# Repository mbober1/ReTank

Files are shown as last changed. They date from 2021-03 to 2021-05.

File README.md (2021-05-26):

# ReTank - DIY remote controlled tank. :blue_car:
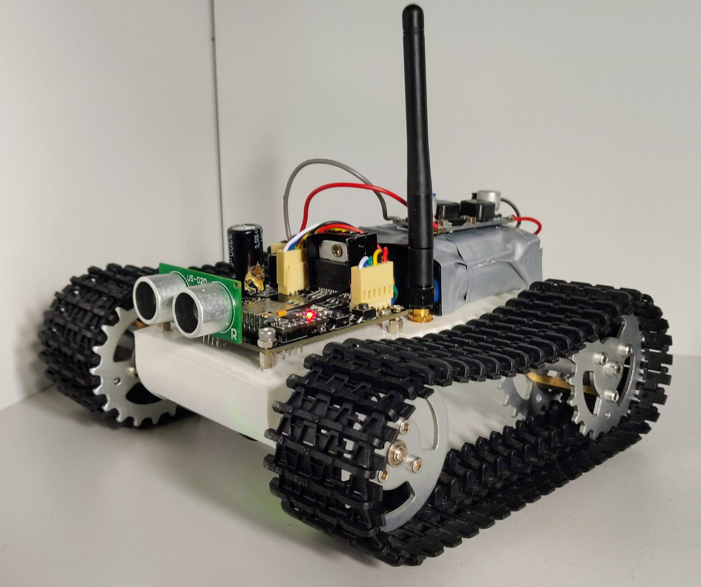
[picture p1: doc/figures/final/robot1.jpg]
alt model


# Usage
## Remote control software
The software controls the robot based on signals sent from the RoboVision program
https://github.com/mbober1/RoboVision

## Features
- [X] DIY energy pack
- [X] WiFi connection
- [X] PID motor power controler
- [X] RoboVision integration
- [X] Circuit board design
- [X] Chassis design

## PCB
Schematic
PCB
PCB2

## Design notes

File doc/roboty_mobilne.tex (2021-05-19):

\documentclass[10pt, a4paper]{article}

\include{preambula}
	
\begin{document}

\def\tablename{Tabela}

\begin{titlepage}
	\begin{center}
		\textsc{\LARGE Projekt}\\[1cm]		
		\textsc{\Large Roboty Mobilne}\\[0.5cm]		
		\rule{\textwidth}{0.08cm}\\[0.4cm]
		{\huge \bfseries Założenia projektowe}\\[1cm]
		{\huge \bfseries Robot gąsienicowy}\\[0.5cm]
		{\huge \bfseries ReTank}\\[0.4cm]
		\rule{\textwidth}{0.08cm}\\[1cm]
		
		\begin{flushright} \large
		\emph{Przygotował:}\\
		Marcin Bober, 249426
		
		\emph{Termin: }srTN18\\[0.4cm]

		\emph{Prowadzący:} \\
		mgr inż. Arkadiusz Mielczarek \\
		
		\end{flushright}
		
		\vfill
		
		{\large \today}
	\end{center}	
\end{titlepage}

\newpage
\tableofcontents
\newpage

\section{Opis projektu}
\label{sec:OpisProjektu}

Projekt dotyczy budowy robota mobilnego, sterowanego zdalnie. 
Zadanie obejmuje zaprojektowanie części elektronicznej, oprogramowania na mikrokontroler i oprogramowania na urządzenie sterujące. 
W skład części elektronicznej wchodzi projekt płytki drukowanej i banku energii.

\section{Bank energii}

\subsection{Ogniwa}

Zasilania robotowi zapewniać będą trzy ogniwa 16850. 
Aby minimalzować koszty, zostały one pozyskane ze starej baterii z laptopa. 
Nie są one dobrze opisane co sprawia że nie jestem w stanie odnaleźć ich specyfikacji.
Ich żywotność również jest nie znana, co uniemożliwia oszacowanie ich łącznej pojemności.

\begin{figure}[H]
	\centering
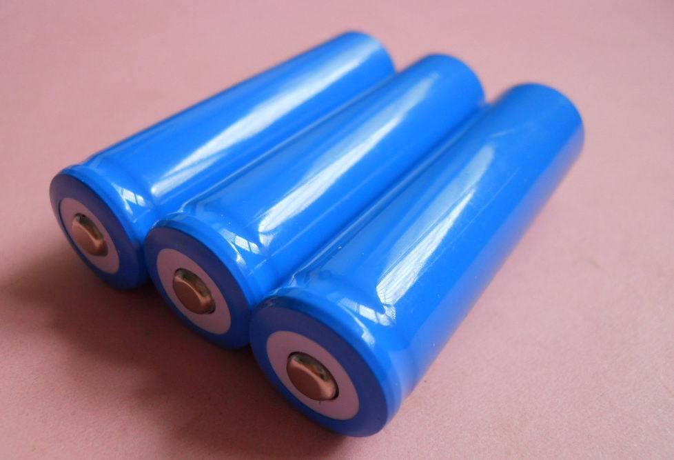
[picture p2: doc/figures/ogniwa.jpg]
	
	\caption{Ogniwa 16850}
	\label{fig:ogniwa}
\end{figure}

\subsection{Balanser}

Do zarządzania ogniwami użyty zostanie gotowy układ BMS przystosowany do współpracy z trzema ogniwami 16850. 
Zapewnia on podstawowe zabezpieczenia w tym:

\begin{itemize}
	\item zabezpieczenie przed nadmiernym rozładowaniem poniżej 3.0V,
	\item zabezpieczenie przed przeładowaniem powyżej 4.25V,
	\item zabezpieczenie przed przeciążeniem prądowym,
	\item zabezpieczenie przed zwarciem.
\end{itemize}

Napięcie generowane przez baterię ogniw powinno oscylować w zakresie 9.0V - 12.7V

\begin{figure}[H]
	\centering
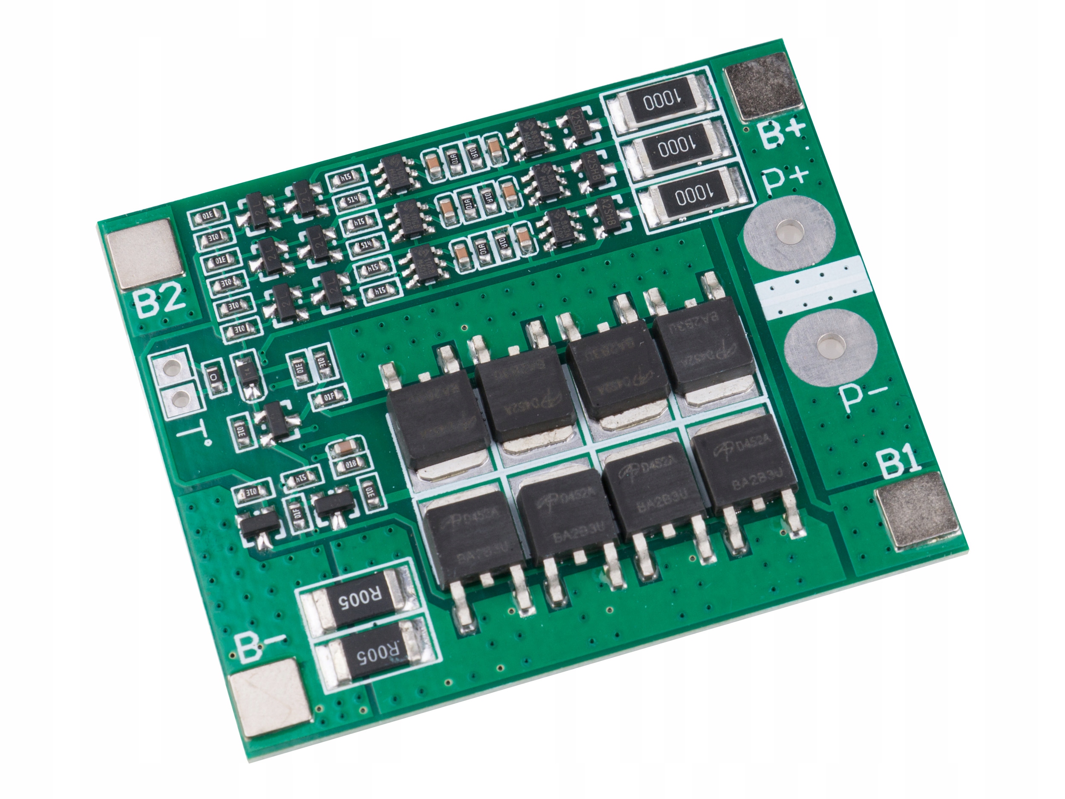
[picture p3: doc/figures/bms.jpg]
	
	\caption{Balanser baterii}
	\label{fig:bms}
\end{figure}

\section{Płytka drukowana}
Jednym z podstawowych elementów projektu jest stworzenie płytki drukowanej integrującej wszystkie wymagane elementy.

\subsection{Mikrokontroler}
Sercem układu zostanie układ ESP32-WROVER. 
Najważniejszym kryterium decydującym o wyborze tego konkretnego układu jest wbudowany modu WiFi i jego niska cena oscylująca w okolicach 2.50\$.
Jest to zdecydowanie najtańszy sposób na połączenia robota do Internetu.

\begin{figure}[H]
	\centering
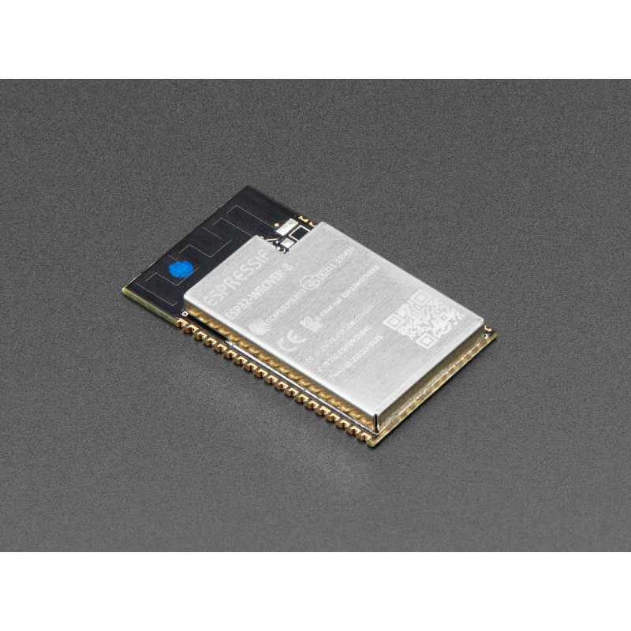
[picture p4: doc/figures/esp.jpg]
	
	\caption{Mikrokontroler ESP32}
	\label{fig:esp32}
\end{figure}

Najważniejsze cechy:
\begin{itemize}
	\item Wbudowany MCU o dwóch rdzeniach z taktowaniem do 240 MHz
	\item Protokoły Wi-Fi: 802.11 b/g/n/d/e/i/k/r
	\item Protokoły BT: Bluetooth v4.2 BR/EDR oraz Bluetooth BLE
	\item Napięcie zasilania: 2.2 V - 3.6 V
	\item Średni pobór prądu: 80 mA
\end{itemize}

\subsection{Sterowniki silników}
Układ będzie wspierał sterowanie dwoma silnikami prądu stałego. 
Każdy z nich będzie mógłbyć wyposarzony w osobny enkoder liczący obroty silnika.
Do tego celu posłuży układa L298N w obudowie Multiwatt 15 pin.

\begin{figure}[H]
	\centering
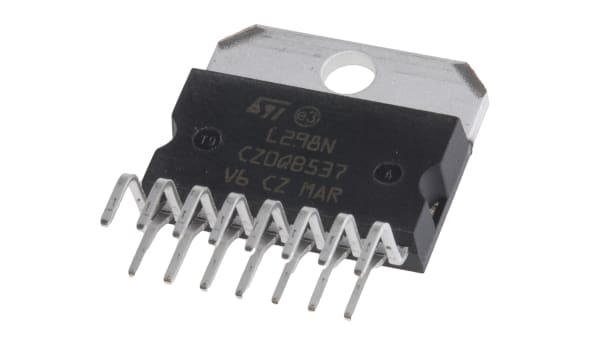
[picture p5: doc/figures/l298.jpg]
	
	\caption{Układ scalony L298N}
	\label{fig:l298n}
\end{figure}

\subsection{Akcelereometr}
Robot będzie wyposarzony w akcelerometr i żyroskop, aby móc mierzyć przyspieszenia oraz prędkości kątowe.
Będzie to możliwe dzięki użyciu układu MPU-6050.

\begin{figure}[H]
	\centering
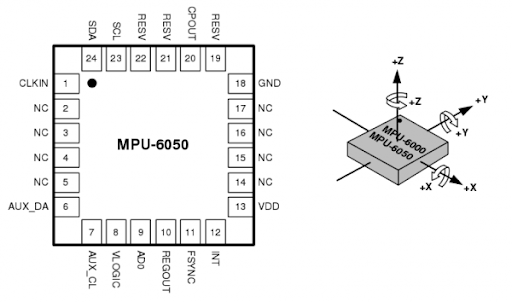
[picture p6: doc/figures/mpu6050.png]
	
	\caption{Układ scalony MPU6050}
	\label{fig:mpu6050}
\end{figure}

\subsection{Inne}
Aby móc komfortowo użytkować i prototypować robota niezbędne będą dodatkowe elementy takie jak:
\begin{itemize}
	\item wyprowadzenie JATG,
	\item wyprowadzenie interfejsu I2C,
	\item wyprowadzenie kamery ArduCam OV2640,
	\item wyprowadzenie UART,
	\item wejście zasilania,
	\item złącze czujnika ultradzwiękowego,
	\item dwa wejścia enkoderów,
	\item dwa wyjścia na silniki.
\end{itemize}

\section{Mechanika}
\subsection{Podwozie}
Aby zredukować koszty i lepiej zintegrować wszystkie elementy ze sobą,
postanowiłem samemu zaprojektować podwozie i wydrukować je przy użyciu drukarki 3D.
Materiał który do tego użyję to ABS.
% Na początku planowania projektu miałem zamiar zaprojektować własne podwozie, 
% ale koszty silników z enkoderami były bardzo duże. Bardziej opłacalne okazały się gotowe zestawy,
% więc zdecydowałem że jako podwozie zostanie użyty zestaw "4WD Smart Robot Car Chassis Kits".
% Jest to najbardziej opłacalne rozwiązanie.

\subsection{Silniki}
Silniki których użyję są produkcji DFRobot. Mają one doczepione enkodery, 
które pozwolą mi bardzo dokładnie kontorlować prędkości silników.
\begin{figure}[H]
	\centering
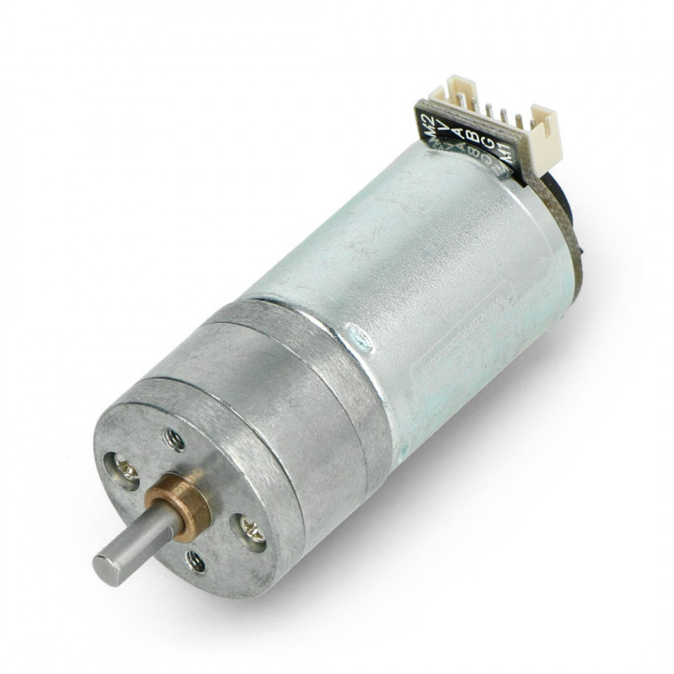
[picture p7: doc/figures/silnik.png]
	
	\caption{Silnik z enkoderem}
	\label{fig:silnk}
\end{figure}

Ich skrócona specyfikacja:
\begin{itemize}
	\item Napięcie zasilania: 6 V
	\item Napięcie enkodera: od 3,3 V do 5 V
	\item Współczynnik redukcji: 1:20
	\item Prędkość bez obciążenia: 300 RPM - 0,1 A
\end{itemize}

\section{Harmonogram}
\begin{enumerate}
	\item Sporządzenie listy i zdobycie wymaganych elementów. (17.03)
	\item Zaprojektowanie i wykonanie podwozia. (24.03)
	\item Zaprojektowanie i wykonanie pakietu baterii. (31.03)
	\item Zaprojektowanie płytki drukowanej. (7.04)
	\item Napisanie i przetestowanie bazowej wersji programu na MCU. (14.04)
	\item Zbudowanie komunikacji z kontrolerem. (21.04)
	\item Dodanie obsługi enkoderów. (28.04)
	\item Dodanie obsługi żyroskopu. (5.05)
	\item Testowanie i dopieszczanie. (12.05)
\end{enumerate}

\section{Podwozie}
Podwozie zostało zaprojektowane w programie Fusion360. 
Pierwsza wersja cierpiała na problemy związane z małą sztywnością 
konstrukcji, co znacząco wpływało na jakość sterowania. 
Z tego też powodu została zaprojektowana druga, znacznie wytrzymalsza
wersja podwozia.

\begin{figure}[H]
	\centering
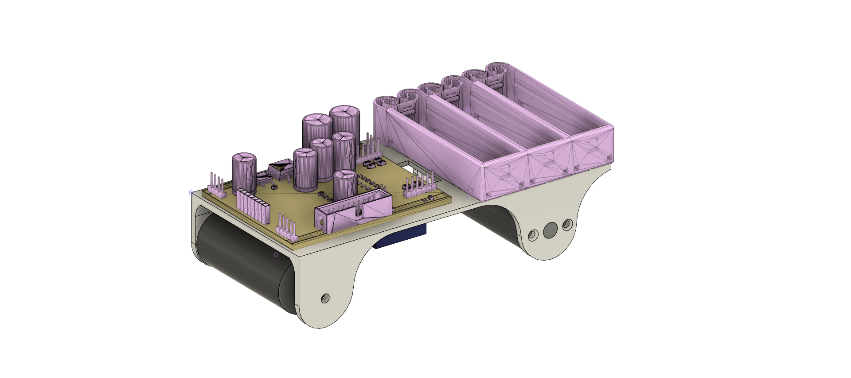
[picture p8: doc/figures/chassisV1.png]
	
	\caption{Pierwsza wersja podwozia}
	\label{fig:chassisv1}
\end{figure}

\begin{figure}[H]
	\centering
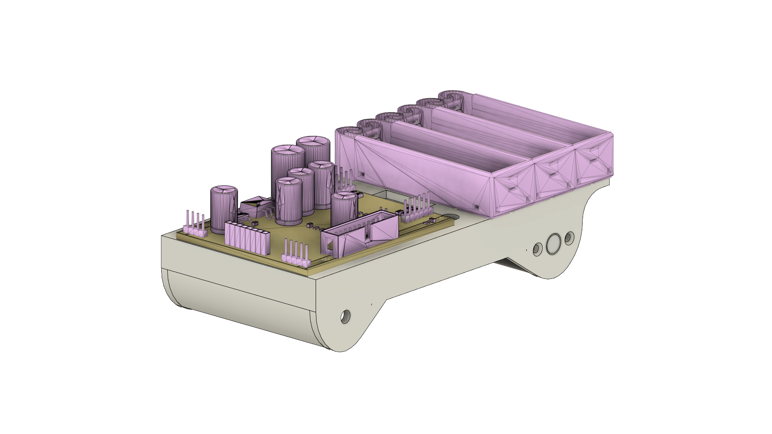
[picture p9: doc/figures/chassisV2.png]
	
	\caption{Druga wersja podwozia}
	\label{fig:chassisv2}
\end{figure}

\section{Płytka drukowana}
W celu zwiększenia jakości i poprawy niezawodności projektu, 
została zaprojektowana płytka drukowana, która ma za zadanie
integrować wszystkie niezbędne peryferia i minimalzować zajmowane miejsce. 

\begin{figure}[H]
	\centering
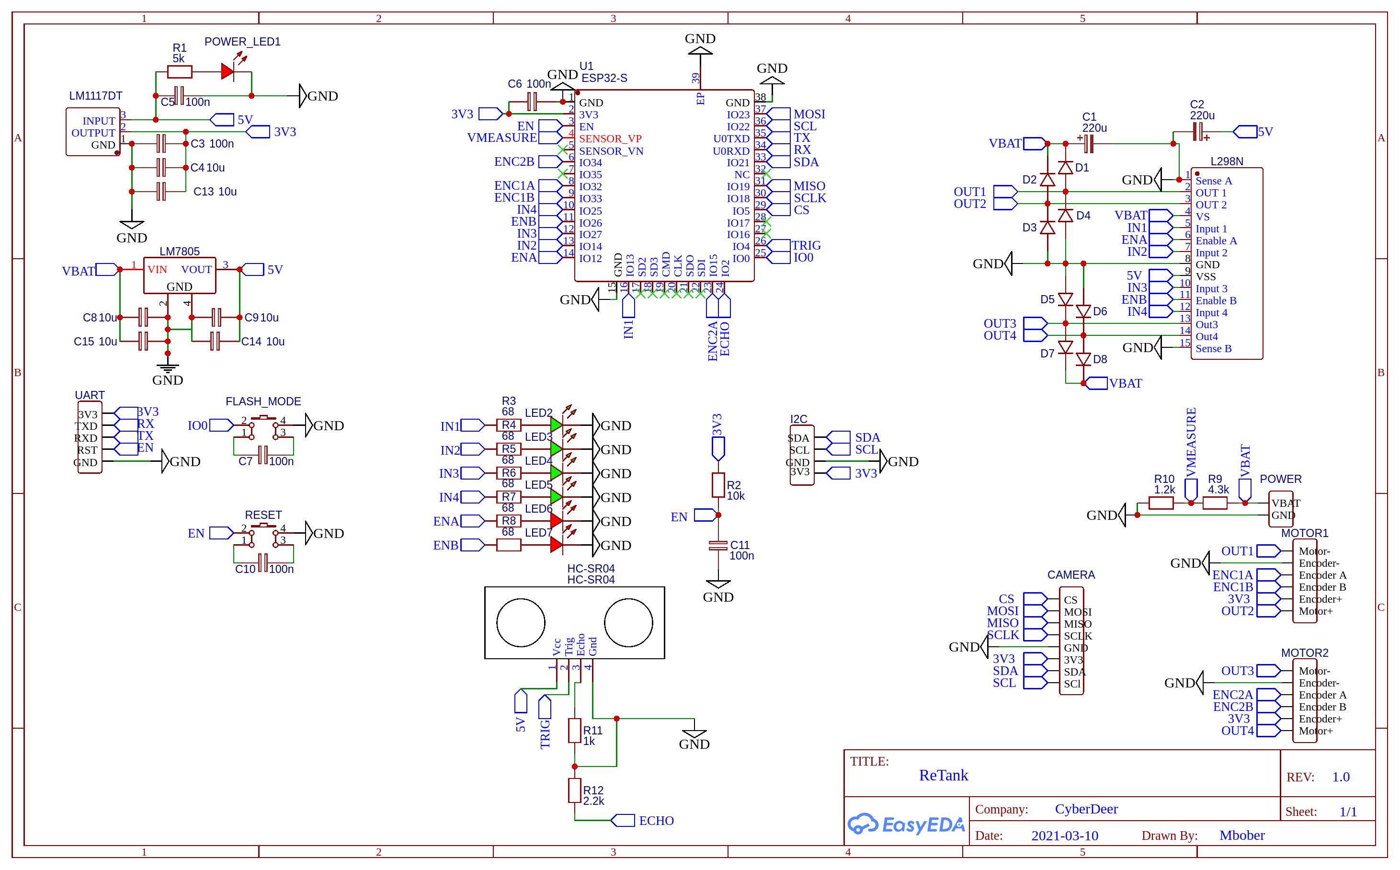
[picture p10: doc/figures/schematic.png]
	
	\caption{Schemat połączeń}
	\label{fig:schematic}
\end{figure}

2021-04-16 zostało złożone zamówienie na 5 sztuk płytek.
Zamówienie jest jeszcze w trakcie transportu. Ostateczną wersję 
można zobaczyć poniżej. Z powodu ograniczonej przestrzeni i
niewystarczającej liczby pinów mikrokontrolera, zrezygnowałem z
portu JTAG.

\begin{figure}[H]
	\centering
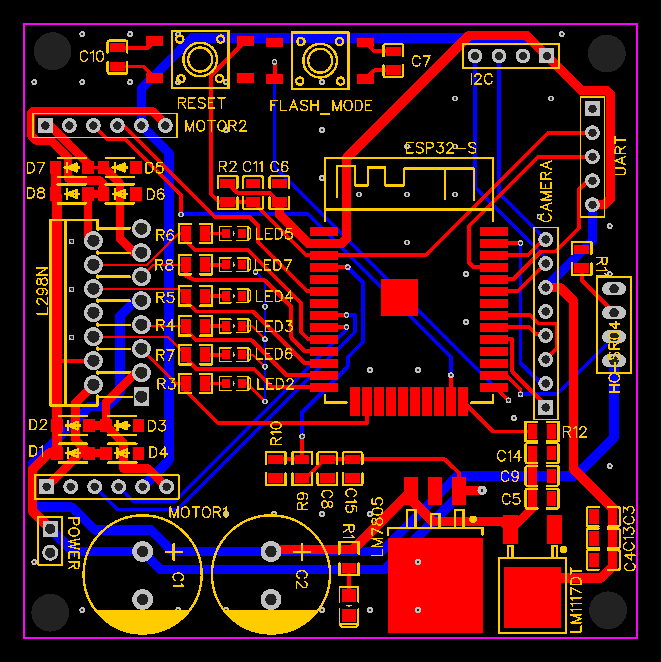
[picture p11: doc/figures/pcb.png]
	
	\caption{PCB}
	\label{fig:pcb}
\end{figure}

\section{Program}
Program na mikrokontroler został napisany z użyciem warstwy abstrakcji
ESP-IDF, udostępnionej przez producenta układu. Dla zwiększenia 
możliwości sprzętu, zdecydowałem się na użycie systemu czasu rzeczywistego
FreeRTOS. Dzięki temu kod został podzielony na oddzielne moduły, 
a każdy z nich pracuje na swoim odrębnym wątku. Pozwoliło to również
ustawiać wyższy piorytet funkcjom, które mają krytyczny wpływ na dzianie robota.
Komunikacja międzyprocesowa została zrealizowana poprzez kolejki piorytetowe,
co znacząco usprawnia cały proces.

Całość kodu dostępna jest w moim repozytorium na
\href{https://github.com/mbober1/ReTank}{GitHub}.

\section{Komunikacja z robotem}

Połączenie z robotem odbywa się poprzez sieć WiFi. W pierwszej kolejności 
nawiązywane jest połączenie przy użyciu protokołu TCP. Jeśli się ono powiedzie
to uruchamiana jest dodatkowa transmicja z wykorzystaniem UDP. 
Dzięki takiej koncepcji mamy dwa niezależne kanały komunikacji. Pierwszy służy
do przesyłania danych które mają niski piorytet czasowy, potrzebują potwierdzenia
odebrania i ewentualnej retransmisji danych. Druga droga komunikacji powstała, 
aby przesyłać ciągły strumień nowych danych. Zależy nam na jaknajniższym opóźnieniu,
a ewentualny błąd trasmisji nie jest krytyczny, bo inforamcje te szybko się 
przedawniają i są zastępowane przez nowe, świeższe. \newline

Każda ramka zaczyna się od wybranej dużej litery alfabetu, określającej rodzaj 
przesyłanych danych. Dla protokołu TCP są to:

	\begin{itemize}
	  \item P - ping,
	  \item D - dystans przeszkody,
	  \item B - bateria,
	  \item S - realna predkość.
	\end{itemize}
	
Natomiast dla protokołu UDP wyróżniamy:
  \begin{itemize}
	\item E - moc silników,
	\item A - akcelometr,
	\item G - żyroskop.
  \end{itemize}

Wszystkie paczki danych zakończone są średnikiem, przed którym znajduje się
ośmiobitowy cykliczny kod nadmiarowy. Niestety ze względu na róźnorodność 
transmitownych informacji, w tym miejscu kończą się cechy wspólne poszczególnych 
ramek.

\subsection{Ping}
Jest to najprostrza z obecych tu ramek. Nie przenosi żadnych informacji.
Oznacza jedynie koniecność odesłania do nadawcy identyczniej wiadomości,
aby można było wyznaczyć chwilę czasowe, niezbędne do obliczenia opóźnienia
transmisji.

Forma ramki to: $P\#;$

Gdzie \# oznacza CRC.

\subsection{Dystans przeszkody}
Przesyła informacje z robota o odległości odczytanej z czujnika ultradzwiękowego.

Forma ramki to: $D<uint8\_t>\#$;
\newline

Gdzie \# oznacza CRC. Przed nim znajduje się wartość odległości wyrażonej 
w centymetrach, w zakresie 0-100cm.

\subsection{Bateria}
Przesyła informacje z robota o poziomie baterii.

Forma ramki to: $B<uint8\_t>\#$;
\newline

Gdzie \# oznacza CRC. Przed nim znajduje się poziom baterii wyrażonej 
w procentach, w zakresie 0-100\%.

\subsection{Prędkość}
Przesyła informacje z robota o prędkości na kołach.

Forma ramki to: $S<uint8\_t> <uint8\_t>\#$;
\newline

Gdzie \# oznacza CRC. Przed nim znajdujdują się dwie wartości oddzielone spacją
odnoszące się do prędkości poszczególnych kół wyrażonej w metrach na sekunde.

\subsection{Moc silników}
Przesyła informacje z aplikacji do robota o zadanej mocy silników.

Forma ramki to: $E<uint8\_t> <uint8\_t>\#$;
\newline

Gdzie \# oznacza CRC. Przed nim znajdujdują się dwie wartości oddzielone spacją
odnoszące się do zadanej mocy poszczególnych kół wyrażonej w procentach.
Zakresy tych wartości musza mieścić się od 0 do 100\%

\subsection{Akcelometr}
Przesyła informacje z robota o aktualnych wskazaniach akcelometru.

Forma ramki to: $A<uint8\_t> <uint8\_t> <uint8\_t>\#$;
\newline

Gdzie \# oznacza CRC. Przed nim znajdujdują się trzy wartości oddzielone spacją
odnoszące się do aktualnych wskazań akcelometru.

\subsection{Żyroskop}
Przesyła informacje z robota o aktualnych wskazaniach żyroskopu.

Forma ramki to: $G<uint8\_t> <uint8\_t> <uint8\_t>\#$;
\newline

Gdzie \# oznacza CRC. Przed nim znajdujdują się trzy wartości oddzielone spacją
odnoszące się do aktualnych wskazań żyroskopu.

\section{Aplikacja do komunikacji}
Rezultaty komunikacji z komputerem i działania całego projektu możemy z
łatwością podziwiać z pomocą mojej specialnie przygotowanej aplikacji w QT
dostępnej w moim repozytorium na
\href{https://github.com/mbober1/RoboVision}{GitHub}.

\begin{figure}[H]
	\centering
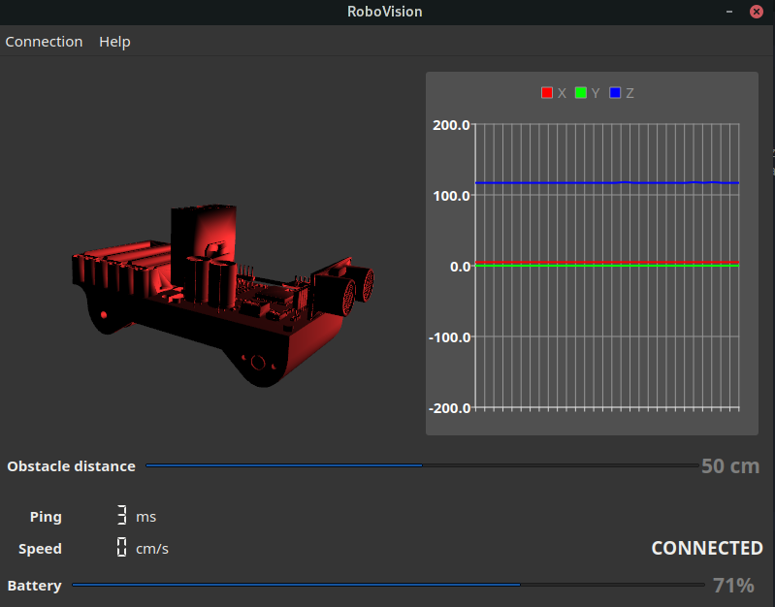
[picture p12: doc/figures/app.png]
	
	\caption{Aplikacja RoboVision}
	\label{fig:app}
\end{figure}

\begin{figure}[H]
	\centering
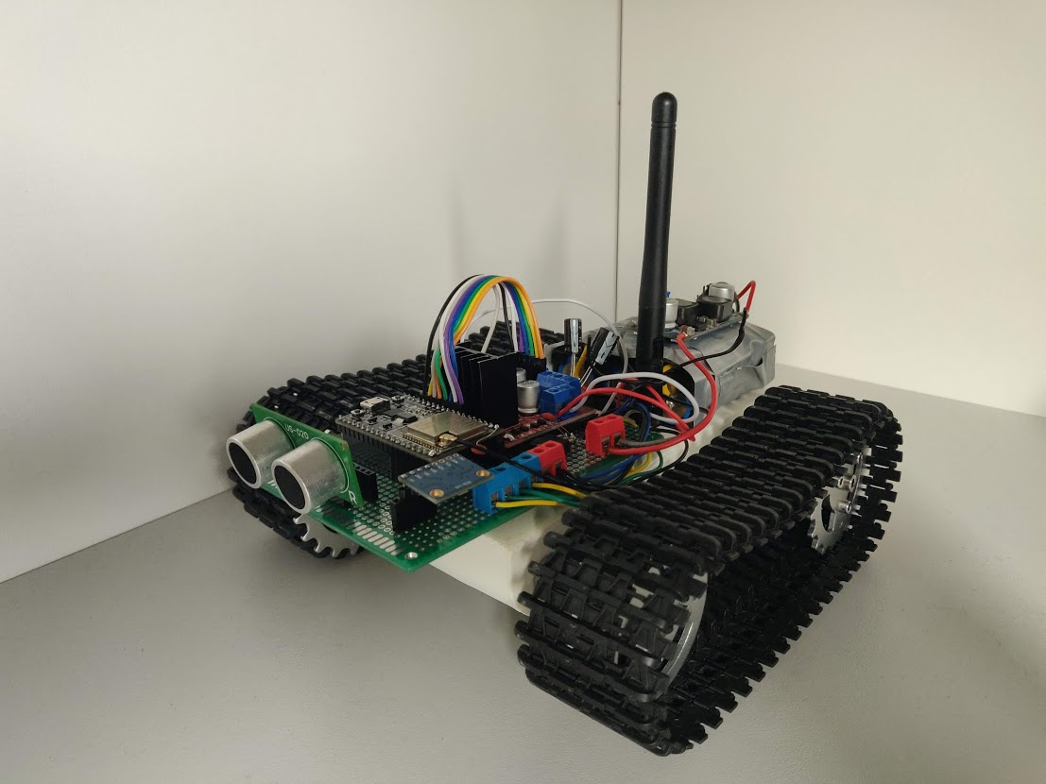
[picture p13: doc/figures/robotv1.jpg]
	
	\caption{Prototyp robota}
	\label{fig:robot}
\end{figure}

\section{Rezultat}
Projekt robota został zakończony sukcesem. Wszystkie problemy z jakimi borykały
się prototypy zostały wyeliminowane. Można więc uznać projekt za zamknięty.  

\begin{figure}[H]
	\centering
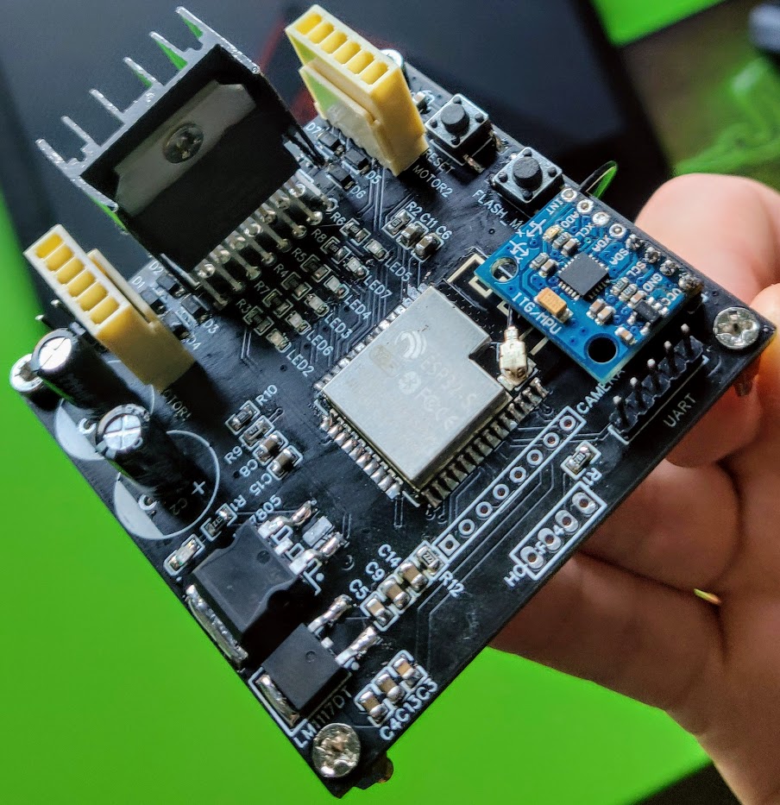
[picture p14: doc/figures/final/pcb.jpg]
	
	\caption{Ostateczna wersja płytki drukowanej}
	\label{fig:pcb_final}
\end{figure}

\begin{figure}[H]
	\centering
	
	\caption{Ostateczna wersja robota}
	\label{fig:robot_final1}
\end{figure}

\begin{figure}[H]
	\centering
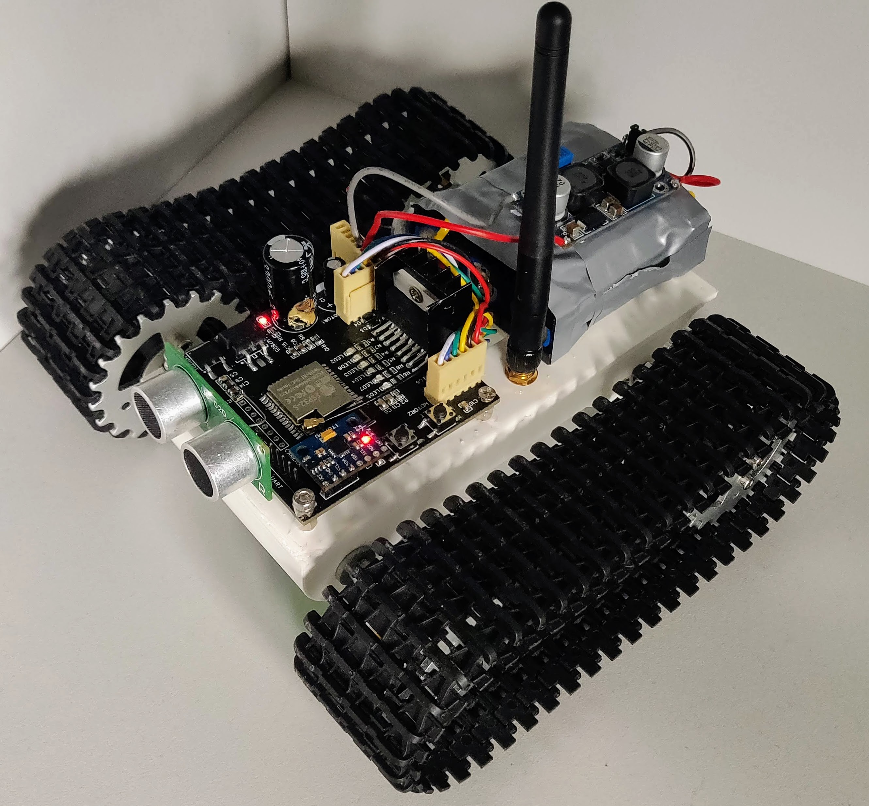
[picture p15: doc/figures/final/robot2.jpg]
	
	\caption{Ostateczna wersja robota}
	\label{fig:robot_final2}
\end{figure}

\begin{figure}[H]
	\centering
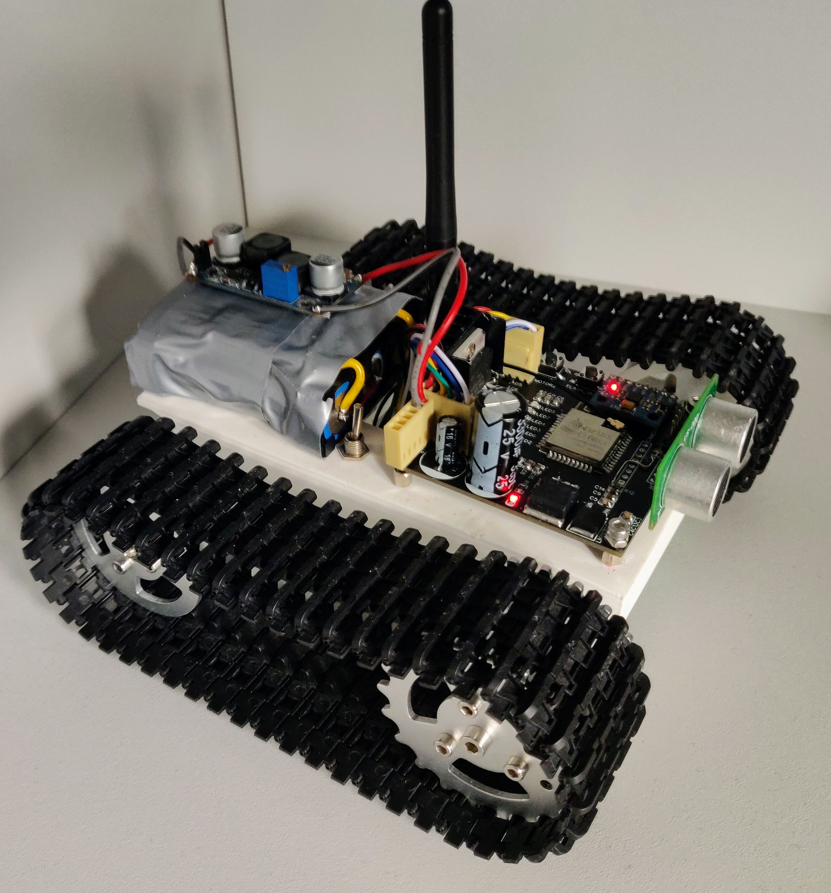
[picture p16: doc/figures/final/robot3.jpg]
	
	\caption{Ostateczna wersja robota}
	\label{fig:robot_final3}
\end{figure}

\begin{figure}[H]
	\centering
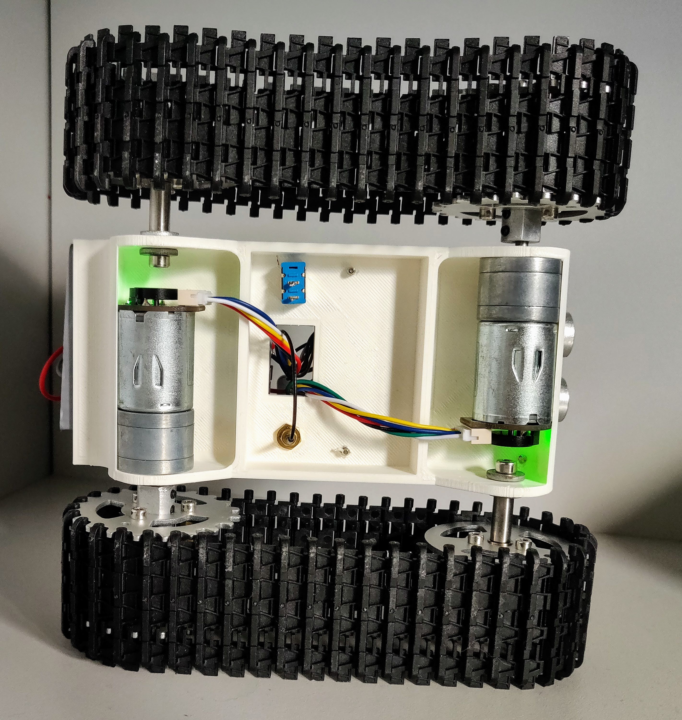
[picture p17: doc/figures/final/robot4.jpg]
	
	\caption{Ostateczna wersja robota}
	\label{fig:robot_final4}
\end{figure}

\end{document}

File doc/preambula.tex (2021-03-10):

%Preambuła dokumentu

% linki w spisie tresci, bibliografi
\usepackage[bookmarks=true,bookmarksnumbered=false,unicode=true,pdftex=true, colorlinks,filecolor=black,linkcolor=black,urlcolor=black,citecolor=black]{hyperref}

%ustawienie rozmiaru papieru
\usepackage[a4paper, left=2.5cm, right=2.5cm, top=2.5cm, bottom=2.5cm, headsep=1.2cm]{geometry}

%rozmaite ustawienia pozwalające okreslić język

%NALEŻY wybrać jeden z pakietów
%\usepackage{polski} %przydatne podczas składania dokumentów w j. polskim
\usepackage[polish]{babel}  % pakiet lokalizujący dokument w języku polskim
%\usepackage[british]{babel}

\usepackage{indentfirst}	% polski styl pisania (np. rozpoczecie pierwszego akapitu
% pod nazwa rozdzialu od wciecia)
%\usepackage[OT4]{fontenc}
\usepackage[utf8]{inputenc} % w miejsce utf8 można wpisać latin2 bądź cp1250,
% w zależności od tego w jaki sposób kodowane są 
% polskie znaki diakrytyczne przy wprowadzaniu 
% z klawiatury.
%kodowanie znaków, zależne od systemu
\usepackage[T1]{fontenc} %poprawne składanie polskich czcionek

%OPEROWANIE NA OBRAZACH
\usepackage{graphicx}       % pakiet graficzny, umożliwiający m.in.
% import grafik w formacie eps
%\usepackage{epstopdf}		% pozwala na importowanie grafik w formacie eps
% przy użyciu pdflatex
\usepackage[update,prepend]{epstopdf}
\usepackage{rotating}       % pakiet umożliwiający obracanie rysunków
\usepackage{subfigure}      % pakiet umożliwiający tworzenie podrysunków
\usepackage{epic}           % pakiet umożliwiający rysowanie w środowisku latex
\usepackage{psfrag}         % pakiet umożliwiający podmianę łańcuchów znaków 
% w plikach eps
%\usepackage{curves}         % pakiet do wykreslania krzywych

%pakiety dodające dużo dodatkowych poleceń matematycznych
\usepackage{amsfonts}       % pakiet z rozmaitymi czcionkami matematycznymi
%\usepackage{amssymb}        % pakiet z rozmaitymi symbolami matematycznymi
\usepackage{amsmath}        % pakiet z rozmaitymi środowiskami matematycznymi

\usepackage{fp}             % pakiet z funkcjami operujacymi 
% na liczbach zmiennoprzecinkowych
\usepackage{calc}           % pakiet umożliwiający operacje arytmetyczne
% na tzw. licznikach (liczbach całkowitych)
\usepackage{leftidx}		% indeksy górne i dolne po lewej stronie

%definicje matematyczne
\providecommand{\abs}[1]{\lvert#1\rvert}
\providecommand{\norm}[1]{\lVert#1\rVert}

%pakiety wspomagające i poprawiające składanie tabel
\usepackage{supertabular}
\usepackage{array}
\usepackage{tabularx}
\usepackage{hhline}
\usepackage{longtable}		% wsparcie dla dlugich tabel
\usepackage{multicol}		% podzial strony na wiele kolumn

%pakiet do BibTex
\usepackage{cite}

\usepackage{url} %pakiet pozawalający na dodawanie adresów url w bibliografi

%pakiet wypisujący na marginesie etykiety równań i rysunków zdefiniowanych przez \label{}, chcąc wygenerować finalną wersję dokumentu wystarczy usunąć poniższą linię
%\usepackage{showlabels}

\usepackage{float}			% lepsza obsluga mechanizmow obiektow plywajacych
% wymuszenie wstawienia np. tabeli, obrazka w danym miejscu przez [H]

\usepackage{listings}       % pakiet dedykowany zrodlom programow
\usepackage{color}

\definecolor{dkgreen}{rgb}{0,0.6,0}
\definecolor{gray}{rgb}{0.5,0.5,0.5}
\definecolor{mauve}{rgb}{0.58,0,0.82}

\lstset{ %
	language=C,                % the language of the code
	basicstyle=\small,           % the size of the fonts that are used for the code
	numbers=left,                   % where to put the line-numbers
	numberstyle=\footnotesize\color{gray},  % the style that is used for the line-numbers
	stepnumber=1,                   % the step between two line-numbers. If it's 1, each line 
	% will be numbered
	numbersep=5pt,                  % how far the line-numbers are from the code
	backgroundcolor=\color{white},      % choose the background color. You must add \usepackage{color}
	showspaces=false,               % show spaces adding particular underscores
	showstringspaces=false,         % underline spaces within strings
	showtabs=false,                 % show tabs within strings adding particular underscores
	%frame=single,                   % adds a frame around the code
	rulecolor=\color{black},        % if not set, the frame-color may be changed on line-breaks within not-black text (e.g. comments (green here))
	tabsize=2,                      % sets default tabsize to 2 spaces
	captionpos=b,                   % sets the caption-position to bottom
	breaklines=true,                % sets automatic line breaking
	breakatwhitespace=false,        % sets if automatic breaks should only happen at whitespace
	%title=\lstname,                   % show the filename of files included with \lstinputlisting;
	% also try caption instead of title
	keywordstyle=\color{blue},          % keyword style
	commentstyle=\color{dkgreen},       % comment style
	stringstyle=\color{mauve},         % string literal style
	escapeinside={\%*}{*)},            % if you want to add LaTeX within your code
	morekeywords={*,...},              % if you want to add more keywords to the set
	deletekeywords={...}              % if you want to delete keywords from the given language
}

%polish signs in lst code
\lstset{literate=%
	{ą}{{\k{a}}}1
	{ć}{{\'c}}1
	{ę}{{\k{e}}}1
	{ł}{{\l}}1
	{ń}{{\'n}}1
	{ó}{{\'o}}1
	{ś}{{\'s}}1
	{ż}{{\.z}}1
	{ź}{{\'z}}1
	{Ą}{{\k{A}}}1
	{Ć}{{\'C}}1
	{Ę}{{\k{E}}}1
	{Ł}{{\L}}1
	{Ń}{{\'N}}1
	{Ó}{{\'O}}1
	{Ś}{{\'S}}1
	{Ż}{{\.Z}}1
	{Ź}{{\'Z}}1
}

\usepackage{verbatim}       % pakiet dedykowany rozmaitym wydrukom tekstowym
\usepackage{ifthen}         % pakiet umożliwiający tworzenie prostych programów
% (m.in. zawiera instrukcje powtórzeniowe 
% i warunkowe)
\usepackage{upquote}		%normal quotations marks ' and `

% deklaracje wymagane przez pakiet theorem automatycznie ladowany w przypadku
% klasy dokumentu article
%
\newtheorem{Dn}{Definicja}[section]     % deklaracja srodowiska definicja
\newtheorem{La}[Dn]{Lemat}                % deklaracja srodowiska lemat
\newtheorem{Tm}[Dn]{Twierdzenie}          % deklaracja srodowiska twierdzenie
\newtheorem{Rk}[Dn]{Spostrze{\.z}enie}  % deklaracja srodowiska spostrzezenie
\newtheorem{Am}[Dn]{Algorytm}           % deklaracja srodowiska algorytm
\newtheorem{As}[Dn]{Za{\l}o{\.z}enie}   % deklaracja srodowiska zalozenie
\newtheorem{Pn}[Dn]{Propozycja}           % deklaracja srodowiska propozycja
\newtheorem{Py}[Dn]{W{\l}asno{\'s}{\'c}}  % deklaracja srodowiska wlasnosc
\newtheorem{Cy}[Dn]{Wniosek}              % deklaracja srodowiska wniosek
\newtheorem{Ee}[Dn]{Przyk{\l}ad}        % deklaracja srodowiska przyklad
\newtheorem{Ex}{{\'C}wiczenie}          % deklaracja srodowiska cwiczenie

%helps to specify width of a column in table
%\begin{tabular}{|C{1cm}|c|c|c|c|c|c|c|c|c|c|}
%first column will have widht of 1cm
\newcolumntype{L}[1]{>{\raggedright\let\newline\\\arraybackslash\hspace{0pt}}m{#1}}
\newcolumntype{C}[1]{>{\centering\let\newline\\\arraybackslash\hspace{0pt}}m{#1}}
\newcolumntype{R}[1]{>{\raggedleft\let\newline\\\arraybackslash\hspace{0pt}}m{#1}}

\sloppy			%zawija bardzo długie linie

%\pagenumbering{gobble}% Remove page numbers (and reset to 1)

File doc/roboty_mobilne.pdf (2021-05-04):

Projekt

Roboty Mobilne

# Założenia projektowe

# Robot gąsienicowy

# ReTank

Przygotował:
Marcin Bober, 249426
Termin: srTN18

Prowadzący:
mgr inż. Arkadiusz Mielczarek

4 maja 2021

## Spis treści

1 Opis projektu | 2
2 Bank energii | 2
3 Płytka drukowana | 3
4 Mechanika | 5
5 Harmonogram | 6
6 Podwozie | 6
7 Płytka drukowana | 7
8 Program | 8
9 Komunikacja z robotem | 8
10 Aplikacja do komunikacji | 10
11 Aktualne rezultaty | 10

## 1 Opis projektu

Projekt dotyczy budowy robota mobilnego, sterowanego zdalnie. Zadanie obejmuje zaprojektowanie części elektronicznej, oprogramowania na mikrokontroler i oprogramowania na urządzenie sterujące. W skład części elektronicznej wchodzi projekt płytki drukowanej i banku energii.

## 2 Bank energii

### 2.1 Ogniwa

Zasilania robotowi zapewniać będą trzy ogniwa 16850. Aby minimalzować koszty, zostały one pozyskane ze starej baterii z laptopa. Nie są one dobrze opisane co sprawia że nie jestem w stanie odnaleźć ich specyfikacji. Ich żywotność również jest nie znana, co uniemożliwia oszacowanie ich łącznej pojemności.


Rysunek 1: Ogniwa 16850

### 2.2 Balanser

Do zarządzania ogniwami użyty zostanie gotowy układ BMS przystosowany do współpracy z trzema ogniwami 16850. Zapewnia on podstawowe zabezpieczenia w tym:

- zabezpieczenie przed nadmiernym rozładowaniem poniżej 3.0V,
- zabezpieczenie przed przeładowaniem powyżej 4.25V,
- zabezpieczenie przed przeciążeniem prądowym,
- zabezpieczenie przed zwarciem.

Napięcie generowane przez baterię ogniw powinno oscylować w zakresie 9.0V - 12.7V


Rysunek 2: Balanser baterii

## 3 Płytka drukowana

Jednym z podstawowych elementów projektu jest stworzenie płytki drukowanej integrującej wszystkie wymagane elementy.

### 3.1 Mikrokontroler

Sercem układu zostanie układ ESP32-WROVER. Najważniejszym kryterium decydującym o wyborze tego konkretnego układu jest wbudowany modu WiFi i jego niska cena oscylująca w okolicach 2.50$. Jest to zdecydowanie najtańszy sposób na połączenia robota do Internetu.


Rysunek 3: Mikrokontroler ESP32

Najważniejsze cechy:

- Wbudowany MCU o dwóch rdzeniach z taktowaniem do 240 MHz
- Protokoły Wi-Fi: 802.11 b/g/n/d/e/i/k/r
- Protokoły BT: Bluetooth v4.2 BR/EDR oraz Bluetooth BLE
- Napięcie zasilania: 2.2 V - 3.6 V
- Średni pobór prądu: 80 mA

### 3.2 Sterowniki silników

Układ będzie wspierał sterowanie dwoma silnikami prądu stałego. Każdy z nich będzie mógłbyć wyposarzony w osobny enkoder liczący obroty silnika. Do tego celu posłuży układa L298N w obudowie Multiwatt 15 pin.


Rysunek 4: Układ scalony L298N

### 3.3 Akcelereometr

Robot będzie wyposarzony w akcelerometr i żyroskop, aby móc mierzyć przyspieszenia oraz prędkości kątowe. Będzie to możliwe dzięki użyciu układu MPU-6050.

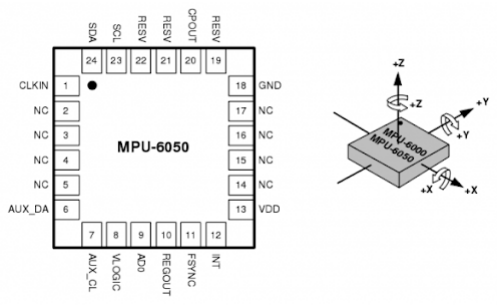
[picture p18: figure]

Rysunek 5: Układ scalony MPU6050

### 3.4 Inne

Aby móc komfortowo użytkować i prototypować robota niezbędne będą dodatkowe elementy takie jak:

- wyprowadzenie JATG,
- wyprowadzenie interfejsu I2C,
- wyprowadzenie kamery ArduCam OV2640,
- wyprowadzenie UART,
- wejście zasilania,
- złącze czujnika ultradzwiękowego,
- dwa wejścia enkoderów,
- dwa wyjścia na silniki.

## 4 Mechanika

### 4.1 Podwozie

Aby zredukować koszty i lepiej zintegrować wszystkie elementy ze sobą, postanowiłem samemu zaprojektować podwozie i wydrukować je przy użyciu drukarki 3D. Materiał który do tego użyję to ABS.

### 4.2 Silniki

Silniki których użyję są produkcji DFRobot. Mają one doczepione enkodery, które pozwolą mi bardzo dokładnie kontorlować prędkości silników.


Rysunek 6: Silnik z enkoderem

Ich skrócona specyfikacja:

- Napięcie zasilania: 6 V
- Napięcie enkodera: od 3,3 V do 5 V
- Współczynnik redukcji: 1:20
- Prędkość bez obciążenia: 300 RPM - 0,1 A

## 5 Harmonogram

1. Sporządzenie listy i zdobycie wymaganych elementów. (17.03)
2. Zaprojektowanie i wykonanie podwozia. (24.03)
3. Zaprojektowanie i wykonanie pakietu baterii. (31.03)
4. Zaprojektowanie płytki drukowanej. (7.04)
5. Napisanie i przetestowanie bazowej wersji programu na MCU. (14.04)
6. Zbudowanie komunikacji z kontrolerem. (21.04)
7. Dodanie obsługi enkoderów. (28.04)
8. Dodanie obsługi żyroskopu. (5.05)
9. Testowanie i dopieszczanie. (12.05)

## 6 Podwozie

Podwozie zostało zaprojektowane w programie Fusion360. Pierwsza wersja cierpiała na problemy związane z małą sztywnością konstrukcji, co znacząco wpływało na jakość sterowania. Z tego też powodu została zaprojektowana druga, znacznie wytrzymalsza wersja podwozia.

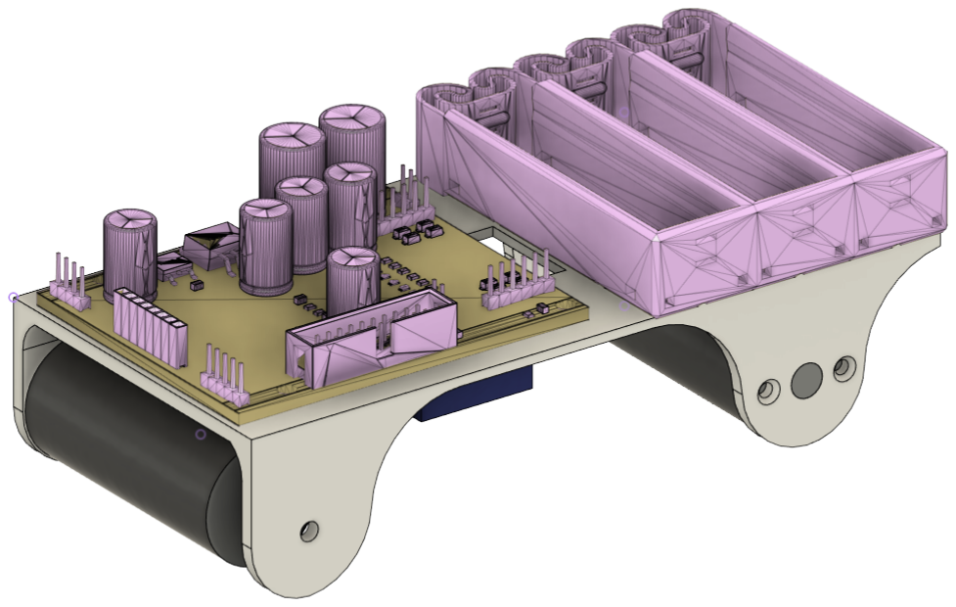
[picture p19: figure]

Rysunek 7: Pierwsza wersja podwozia

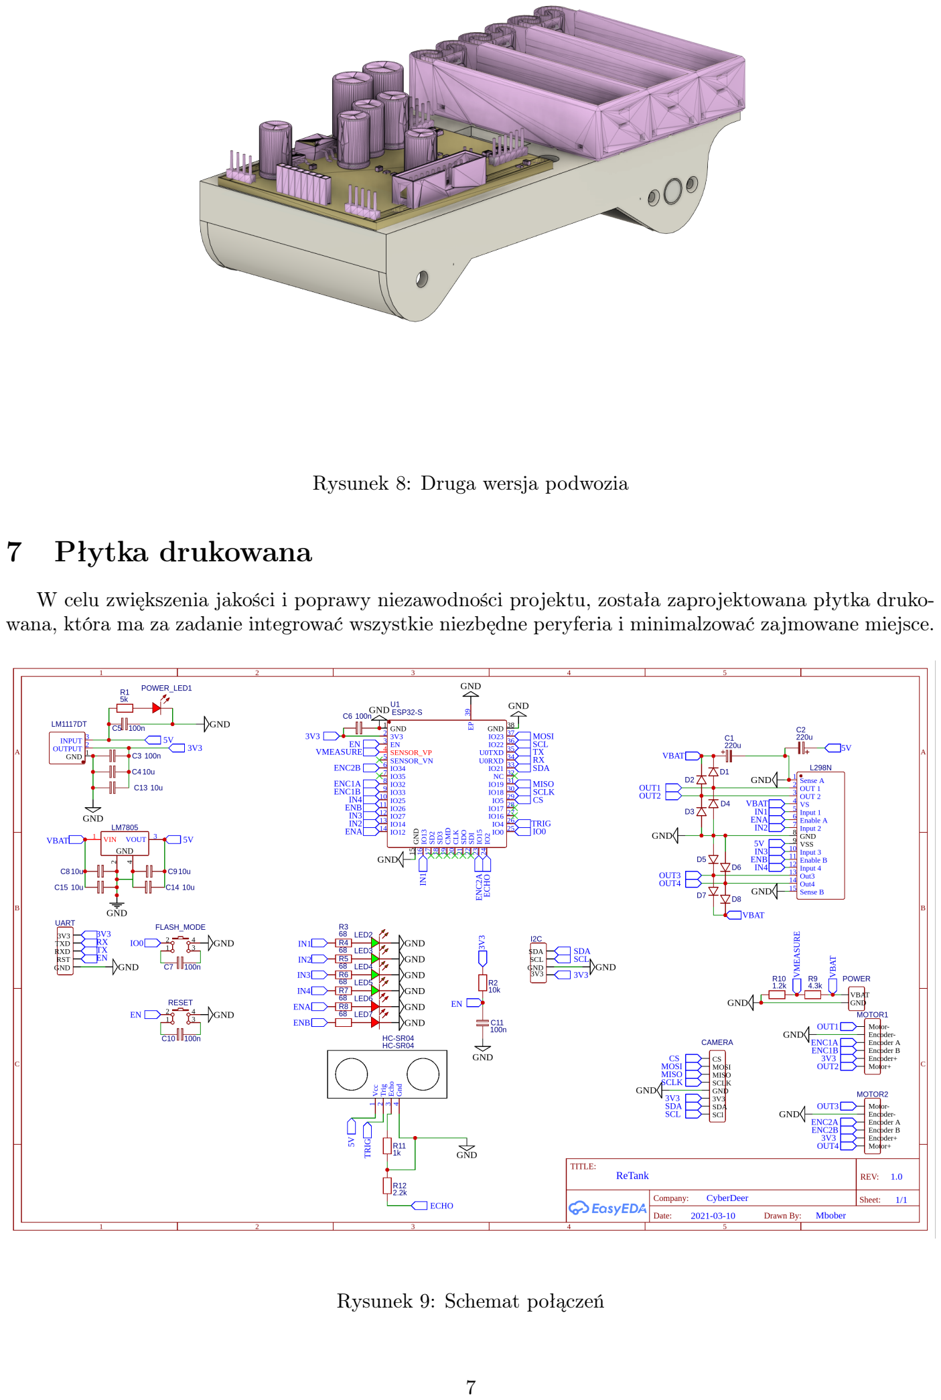
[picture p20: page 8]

Rysunek 8: Druga wersja podwozia

## 7 Płytka drukowana

W celu zwiększenia jakości i poprawy niezawodności projektu, została zaprojektowana płytka drukowana, która ma za zadanie integrować wszystkie niezbędne peryferia i minimalzować zajmowane miejsce.

Rysunek 9: Schemat połączeń

2021-04-16 zostało złożone zamówienie na 5 sztuk płytek. Zamówienie jest jeszcze w trakcie transportu. Ostateczną wersję można zobaczyć poniżej. Z powodu ograniczonej przestrzeni i niewystarczającej liczby pinów mikrokontrolera, zrezygnowałem z portu JTAG.

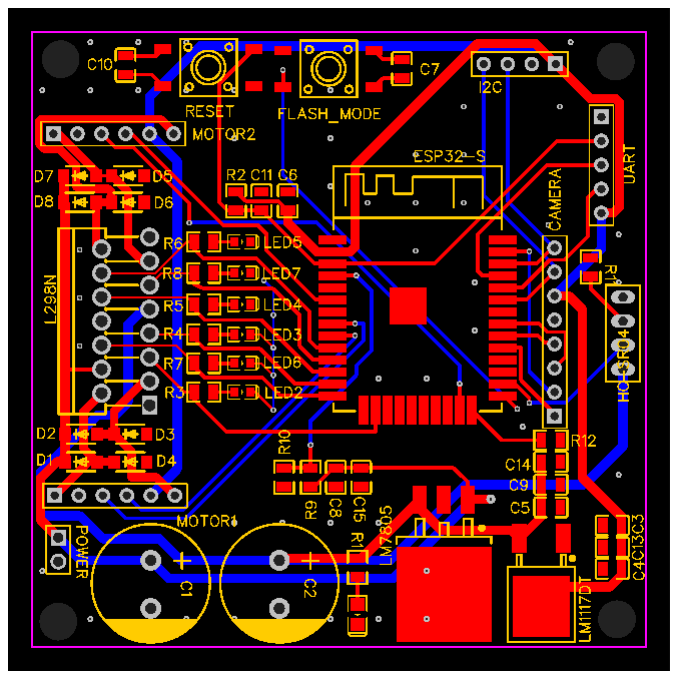
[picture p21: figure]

Rysunek 10: PCB

## 8 Program

Program na mikrokontroler został napisany z użyciem warstwy abstrakcji ESP-IDF, udostępnionej przez producenta układu. Dla zwiększenia możliwości sprzętu, zdecydowałem się na użycie systemu czasu rzeczywistego FreeRTOS. Dzięki temu kod został podzielony na oddzielne moduły, a każdy z nich pracuje na swoim odrębnym wątku. Pozwoliło to również ustawiać wyższy piorytet funkcjom, które mają krytyczny wpływ na dzianie robota. Komunikacja międzyprocesowa została zrealizowana poprzez kolejki piorytetowe, co znacząco usprawnia cały proces.
Całość kodu dostępna jest w moim repozytorium na GitHub. (https://github.com/mbober1/ReTank)

## 9 Komunikacja z robotem

Połączenie z robotem odbywa się poprzez sieć WiFi. W pierwszej kolejności nawiązywane jest połączenie przy użyciu protokołu TCP. Jeśli się ono powiedzie to uruchamiana jest dodatkowa transmicja z wykorzystaniem UDP. Dzięki takiej koncepcji mamy dwa niezależne kanały komunikacji. Pierwszy służy do przesyłania danych które mają niski piorytet czasowy, potrzebują potwierdzenia odebrania i ewentualnej retransmisji danych. Druga droga komunikacji powstała, aby przesyłać ciągły strumień nowych danych. Zależy nam na jaknajniższym opóźnieniu, a ewentualny błąd trasmisji nie jest krytyczny, bo inforamcje te szybko się przedawniają i są zastępowane przez nowe, świeższe.

Każda ramka zaczyna się od wybranej dużej litery alfabetu, określającej rodzaj przesyłanych danych. Dla protokołu TCP są to:

- P - ping,
- D - dystans przeszkody,
- B - bateria,
- S - realna predkość.

Natomiast dla protokołu UDP wyróżniamy:

- E - moc silników,
- A - akcelometr,
- G - żyroskop.

Wszystkie paczki danych zakończone są średnikiem, przed którym znajduje się ośmiobitowy cykliczny kod nadmiarowy. Niestety ze względu na róźnorodność transmitownych informacji, w tym miejscu kończą się cechy wspólne poszczególnych ramek.

### 9.1 Ping

Jest to najprostrza z obecych tu ramek. Nie przenosi żadnych informacji. Oznacza jedynie koniecność odesłania do nadawcy identyczniej wiadomości, aby można było wyznaczyć chwilę czasowe, niezbędne do obliczenia opóźnienia transmisji.
Forma ramki to: P #;
Gdzie # oznacza CRC.

### 9.2 Dystans przeszkody

Przesyła informacje z robota o odległości odczytanej z czujnika ultradzwiękowego.
Forma ramki to: D < uint8_t > #;

Gdzie # oznacza CRC. Przed nim znajduje się wartość odległości wyrażonej w centymetrach, w zakresie 0-100cm.

### 9.3 Bateria

Przesyła informacje z robota o poziomie baterii.
Forma ramki to: B < uint8_t > #;

Gdzie # oznacza CRC. Przed nim znajduje się poziom baterii wyrażonej w procentach, w zakresie 0-100%.

### 9.4 Prędkość

Przesyła informacje z robota o prędkości na kołach.
Forma ramki to: S < uint8_t >< uint8_t > #;

Gdzie # oznacza CRC. Przed nim znajdujdują się dwie wartości oddzielone spacją odnoszące się do prędkości poszczególnych kół wyrażonej w metrach na sekunde.

### 9.5 Moc silników

Przesyła informacje z aplikacji do robota o zadanej mocy silników.
Forma ramki to: E < uint8_t >< uint8_t > #;

Gdzie # oznacza CRC. Przed nim znajdujdują się dwie wartości oddzielone spacją odnoszące się do zadanej mocy poszczególnych kół wyrażonej w procentach. Zakresy tych wartości musza mieścić się od 0 do 100%

### 9.6 Akcelometr

Przesyła informacje z robota o aktualnych wskazaniach akcelometru.
Forma ramki to: A < uint8_t >< uint8_t >< uint8_t > #;

Gdzie # oznacza CRC. Przed nim znajdujdują się trzy wartości oddzielone spacją odnoszące się do aktualnych wskazań akcelometru.

### 9.7 Żyroskop

Przesyła informacje z robota o aktualnych wskazaniach żyroskopu.
Forma ramki to: G < uint8_t >< uint8_t >< uint8_t > #;

Gdzie # oznacza CRC. Przed nim znajdujdują się trzy wartości oddzielone spacją odnoszące się do aktualnych wskazań żyroskopu.

## 10 Aplikacja do komunikacji

Rezultaty komunikacji z komputerem i działania całego projektu możemy z łatwością podziwiać z pomocą mojej specialnie przygotowanej aplikacji w QT dostępnej w moim repozytorium na GitHub. (https://github.com/mbober1/RoboVision)

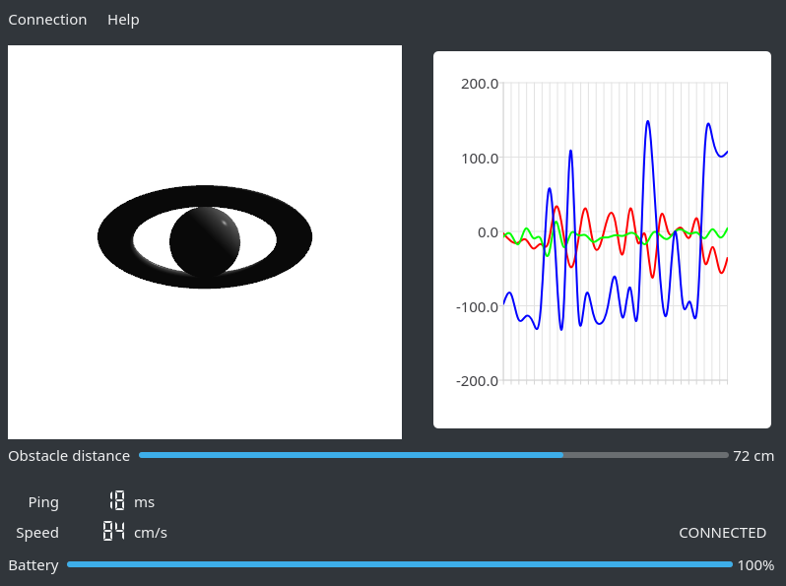
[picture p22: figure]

Rysunek 11: Aplikacja RoboVision

## 11 Aktualne rezultaty

Na dzień dzisiejszy, projekt nie jest obarczony żadnymi opóźnieniami. Wszystkie zaplanowane kamienie milowe zostały osiągnięte przed terminem. Robot może poszczycić się już działającym mi silnikami wraz z sterownikami PID, gotowym czujnikiem ultradzwiękowym, akcelerometrem, żyroskopem, komunikacją z zewnętrzną aplikacją. Pozostało więc jedynie poprawiać pozostałe błędy i czekać na przybycie przesyłki z płytką drukowaną, aby móc skończyć projekt.


Rysunek 12: Prototyp robota

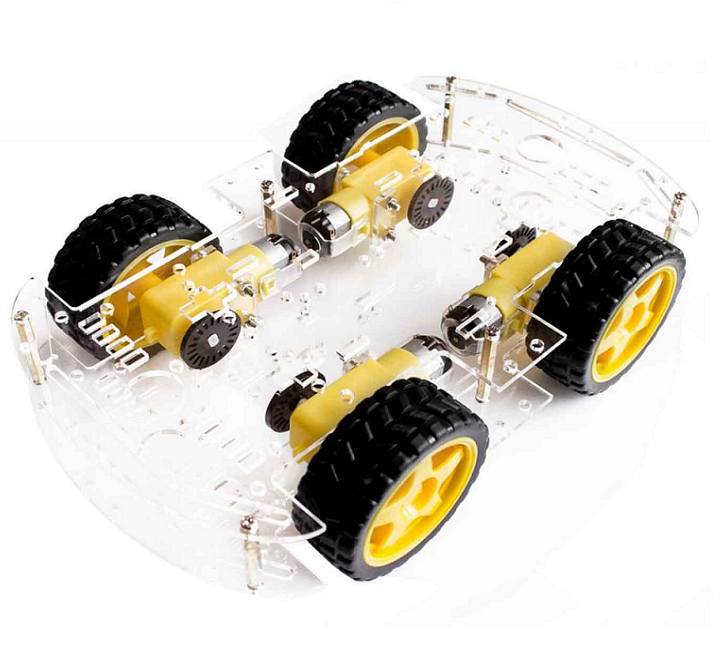
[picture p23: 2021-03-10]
doc/figures/podwozie.png

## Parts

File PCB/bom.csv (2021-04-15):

ID | Name | Designator | Footprint | Quantity | Manufacturer Part | Manufacturer | Supplier | Supplier Part | Price | LCSC Assembly | Assembly Type | Paste Type
1 | 220u | C1,C2 | CAP-D12.5×F5.0 | 2
2 | 10u | C4,C8,C9,C13,C14,C15 | C0805 | 6
3 | 100n | C3,C5,C6,C7,C10,C11 | C0805 | 6
4 | CAMERA HEADER | CAMERA | HDR-F-2.54_1X8 | 1 |  |  | LCSC | C225505 | 0.1815
5 | 1N4007W | D1,D2,D3,D4,D5,D6,D7,D8 | SOD-123_L2.8-W1.8-LS3.7-RD | 8 | 1N4007W | BLUE ROCKET | LCSC | C328592 | 0.0085
6 | ESP32-S | ESP32-S | WIRELM-SMD_ESP32-S | 1 | ESP32-S | Ai-Thinker | LCSC | C277944 | 4.1205 | Yes |  | expand
7 | FLASH MODE | FLASH_MODE | KEY-SMD_4P-L6.0-W6.0-P3.90-LS10.0 | 1 | K2-6639SP-D4SC-04 | 韩国韩荣 | LCSC | C191626 | 0.0375
8 | HC-SR04 | HC-SR04 | HC-SR04 | 1 | HC-SR04
9 | I2C Header | I2C | HDR-M-2.54_1X4 | 1 |  |  | LCSC | C124378 | 0.0261
10 | L298N | L298N | MULTIWATT-15_L19.6-W5.0-P1.27-L | 1 | L298N | STMicroelectronics | LCSC | C19922 | 3.8483 | Yes | manualWeld | expand
11 | LED-0603_G | LED2,LED3,LED4,LED5 | LED0603_GREEN | 4 | 19-217/GHC-YR1S2/3T | EVERLIGHT(台湾亿光) | LCSC | C72043 | 0.0246
12 | LED-0603_R | LED6,LED7 | LED0603_RED | 2 | 19-217/R6C-AL1M2VY/3T | EVERLIGHT(台湾亿光) | LCSC | C72044 | 0.0141
13 | LM1117DT | LM1117DT | TO-252-2_L6.6-W6.1-P4.57-LS9.9-BR-CW | 1 | LM1117DTX-3.3/NOPB | Texas Instruments | LCSC | C73181 | 1.0659 | Yes | smtWeld | expand
14 | LM7805 | LM7805 | TO-263-3_L8.6-W10.2-P2.54-LS14.4-BR | 1 | LM7805CS/TR | HGSEMI(华冠) | LCSC | C725350
15 | MOTOR1 | MOTOR1,MOTOR2 | HDR-M-2.54_1X6 | 2 |  |  | LCSC | C190819 | 0.0185
16 | POWER IN | POWER | HDR-M-2.54_1X2 | 1 |  |  | LCSC | C124375 | 0.0159
17 | LED-0805_R | POWER_LED1 | LED0805_RED | 1 | 17-21SURC/S530-A3/TR8 | EVERLIGHT(台湾亿光) |  | C72037 | 0.0141
18 | 5k | R1 | R0805 | 1
19 | 10k | R2 | R0805 | 1
20 | 68 | R3,R4,R5,R6,R7,R8 | R0805 | 6
21 | 4.3k | R9 | R0805 | 1
22 | 1.2k | R10 | R0805 | 1
23 | 1k | R11 | R0805 | 1
24 | 2.2k | R12 | R0805 | 1
25 | RESET | RESET | KEY-SMD_4P-L6.0-W6.0-P3.90-LS10.0 | 1 | K2-6639SP-D4SC-04 | 韩国韩荣 | LCSC | C191626 | 0.0375
26 | UART | UART | HDR-M-2.54_1X5 | 1 |  |  | LCSC | C358687 | 0.0184

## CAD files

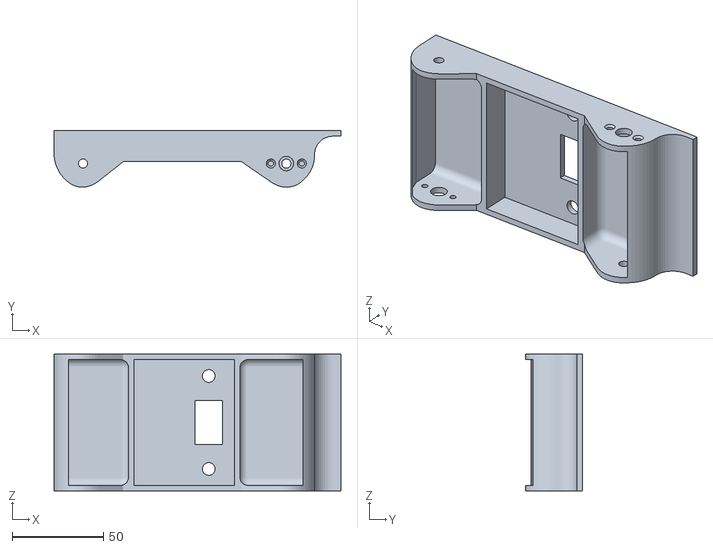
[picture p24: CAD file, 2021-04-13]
3D_MODEL/chassis.stl
157.4 x 31.0 x 75.0

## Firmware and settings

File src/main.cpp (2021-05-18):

#include "tasks.hpp"



extern "C" void app_main()
{
    esp_pm_config_esp32_t power = {};
    power.min_freq_mhz = 240;
    power.max_freq_mhz = 240;
    power.light_sleep_enable = false;
    esp_pm_configure(&power);

    initialise_wifi();

    engineQueue = xQueueCreate(5, sizeof(EnginePacket));
    accelQueue = xQueueCreate(5, sizeof(AcceloPacket));
    gyroQueue = xQueueCreate(5, sizeof(GyroPacket));
    batteryQueue = xQueueCreate(5, sizeof(int));
    distanceQueue = xQueueCreate(5, sizeof(int));
    speedQueue = xQueueCreate(5, sizeof(int16_t));

    
    Ultrasonic sensor(TRIG, ECHO, SENSOR_PWM);



    static const char *TAG = "TCP";
    
    struct sockaddr_storage dest_addr;
    struct sockaddr_in *dest_addr_ip4 = (struct sockaddr_in *)&dest_addr;
    dest_addr_ip4->sin_addr.s_addr = htonl(INADDR_ANY);
    dest_addr_ip4->sin_family = AF_INET;
    dest_addr_ip4->sin_port = htons((int)TCP_PORT);

    int listen_sock = socket(AF_INET, SOCK_STREAM, IPPROTO_IP);

    if (listen_sock < 0) {
        ESP_LOGE(TAG, "Unable to create socket: errno %d", errno);
        vTaskDelete(NULL);
        return;
    }

    int opt = 1;
    setsockopt(listen_sock, SOL_SOCKET, SO_REUSEADDR, &opt, sizeof(opt));

    ESP_LOGI(TAG, "Socket created");

    int err = bind(listen_sock, (struct sockaddr *)&dest_addr, sizeof(dest_addr));
    if(err) {
        ESP_LOGE(TAG, "Socket unable to bind: errno %d", errno);
        ESP_LOGE(TAG, "IPPROTO: %d", AF_INET);
    } else {
        err = listen(listen_sock, 1);
    }

    if(!err) {
        ESP_LOGI(TAG, "Socket bound, port %d", (int)TCP_PORT);

        while (1) {
            ESP_LOGI(TAG, "Socket listening");

            struct sockaddr_storage source_addr;
            socklen_t addr_len = sizeof(source_addr);
            int sock = accept(listen_sock, (struct sockaddr *)&source_addr, &addr_len);
            if (sock < 0) {
                ESP_LOGE(TAG, "Unable to accept connection: errno %d", errno);
                break;
            }

            // Set tcp keepalive option
            int keepAlive = 1;
            int keepIdle = KEEPALIVE_IDLE;
            int keepInterval = KEEPALIVE_INTERVAL;
            int keepCount = KEEPALIVE_COUNT;
            setsockopt(sock, SOL_SOCKET, SO_KEEPALIVE, &keepAlive, sizeof(int));
            setsockopt(sock, IPPROTO_TCP, TCP_KEEPIDLE, &keepIdle, sizeof(int));
            setsockopt(sock, IPPROTO_TCP, TCP_KEEPINTVL, &keepInterval, sizeof(int));
            setsockopt(sock, IPPROTO_TCP, TCP_KEEPCNT, &keepCount, sizeof(int));


            // Convert ip address to string
            char clientAddress[128];
            if (source_addr.ss_family == PF_INET) {
                inet_ntoa_r(((struct sockaddr_in *)&source_addr)->sin_addr, clientAddress, sizeof(clientAddress) - 1);
            }

            printf("%s | Socket %d accepted ip address: %s\n", TAG, sock, clientAddress);

            TaskHandle_t txtcp = NULL;
            TaskHandle_t rxudp = NULL;
            TaskHandle_t txudp = NULL;
            TaskHandle_t driver = NULL;
            TaskHandle_t battery = NULL;
            TaskHandle_t mpu = NULL;

            xTaskCreate(TXtcp, "tcp_client_tx", 4096, (void*)sock, 5, &txtcp);
            xTaskCreate(RXudp, "udp_server_rx", 4096, (void*)UDP_PORT, 10, &rxudp);
            xTaskCreate(robotDriver, "driver", 4096, nullptr, 20, &driver);
            xTaskCreate(batteryTask, "batteryTask", configMINIMAL_STACK_SIZE * 3, NULL, 3, &battery);
            xTaskCreate(mpuTask, "mpuTask", 4096, NULL, 5, &mpu);


            RXtcp(sock); //wait until client connected

            printf("TCP TX kill task \n");
            vTaskDelete(&txtcp);
            vTaskDelete(&txudp);
            vTaskDelete(&rxudp);
            vTaskDelete(&driver);
            vTaskDelete(&battery);
            vTaskDelete(&mpu);
            shutdown(sock, 0);
            close(sock);
        } 
    } else ESP_LOGE(TAG, "Error occurred during listen: errno %d", errno);

    close(listen_sock);
    // vTaskSuspend(NULL);
}

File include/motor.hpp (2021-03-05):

#pragma once
#include <stdint.h>
#include "soc/ledc_struct.h"


enum class Direction {
    FORWARD,
    BACKWARD
};


class motor
{
private:
    uint8_t in1, in2, pwmPin, pwmChannel;
public:
    motor(uint8_t in1, uint8_t in2, uint8_t pwmPin, uint8_t pwmChannel);
    void direction(Direction dir);
    void power(uint8_t pow);
    void fastStop();
    void softStop();
};


motor::motor(uint8_t in1, uint8_t in2, uint8_t pwmPin, uint8_t pwmChannel) : in1(in1), in2(in2), pwmPin(pwmPin), pwmChannel(pwmChannel) {
    pinMode(this->in1, OUTPUT);
    pinMode(this->in2, OUTPUT);
    pinMode(this->pwmPin, OUTPUT);
    ledcSetup(this->pwmChannel, 2000, 8);
    gpio_matrix_out(this->pwmPin, LEDC_HS_SIG_OUT0_IDX + this->pwmChannel, false, false); //attach pin
    softStop();
}


void motor::direction(Direction dir) {
    if(static_cast<uint8_t>(dir)) {
        GPIO.out_w1ts = ((uint32_t)1 << in1);
        GPIO.out_w1tc = ((uint32_t)1 << in2);
    } else {
        GPIO.out_w1tc = ((uint32_t)1 << in1);
        GPIO.out_w1ts = ((uint32_t)1 << in2);
    }
}

void motor::fastStop() {
    GPIO.out_w1ts = ((uint32_t)1 << in1);
    GPIO.out_w1ts = ((uint32_t)1 << in2);
}

void motor::softStop() {
    GPIO.out_w1tc = ((uint32_t)1 << in1);
    GPIO.out_w1tc = ((uint32_t)1 << in2);
}



void motor::power(uint8_t pow) {
    LEDC.channel_group[0].channel[this->pwmChannel].duty.duty = pow << 4;//25 bit (21.4)
    if(pow) {
        LEDC.channel_group[0].channel[this->pwmChannel].conf0.sig_out_en = 1;//This is the output enable control bit for channel
        LEDC.channel_group[0].channel[this->pwmChannel].conf1.duty_start = 1;//When duty_num duty_cycle and duty_scale has been configured. these register won't take effect until set duty_start. this bit is automatically cleared by hardware.
        LEDC.channel_group[0].channel[this->pwmChannel].conf0.clk_en = 1;
    } else {
        LEDC.channel_group[0].channel[this->pwmChannel].conf0.sig_out_en = 0;//This is the output enable control bit for channel
        LEDC.channel_group[0].channel[this->pwmChannel].conf1.duty_start = 0;//When duty_num duty_cycle and duty_scale has been configured. these register won't take effect until set duty_start. this bit is automatically cleared by hardware.
        LEDC.channel_group[0].channel[this->pwmChannel].conf0.clk_en = 0;
    }
}

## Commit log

2021-03-12 retarded PID on ESP-IDF
2021-03-13 real PID
2021-03-18 encoder x2
2021-03-24 i2c + spi
2021-03-24 f spi
2021-03-26 camera init
2021-03-26 camera works!
2021-04-05 battery packet
2021-04-05 battery package fix
2021-04-06 ultrasonic sensor
2021-04-07 ultrasonic cleanup
2021-04-07 encoder work
2021-04-07 disabled pid
2021-04-07 prety good pid
2021-04-07 pid ready
2021-04-12 ultrasonic upgrade
2021-04-12 ultrasonic fix
2021-04-12 adc percentage calculation
2021-04-13 added 3d model of chassis
    [chassis.stl]
2021-04-15 pcb ready
    [Gerber_BoardOutline.GKO, Gerber_BottomLayer.GBL, Gerber_BottomSilkLayer.GBO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]
2021-04-20 pid upgrade
2021-04-20 soft pid
2021-04-26 pid + ultrasonic
2021-05-10 gyro on
2021-05-12 gyro + acc
